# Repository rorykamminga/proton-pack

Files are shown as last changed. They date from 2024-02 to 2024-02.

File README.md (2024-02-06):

# Proton Pack
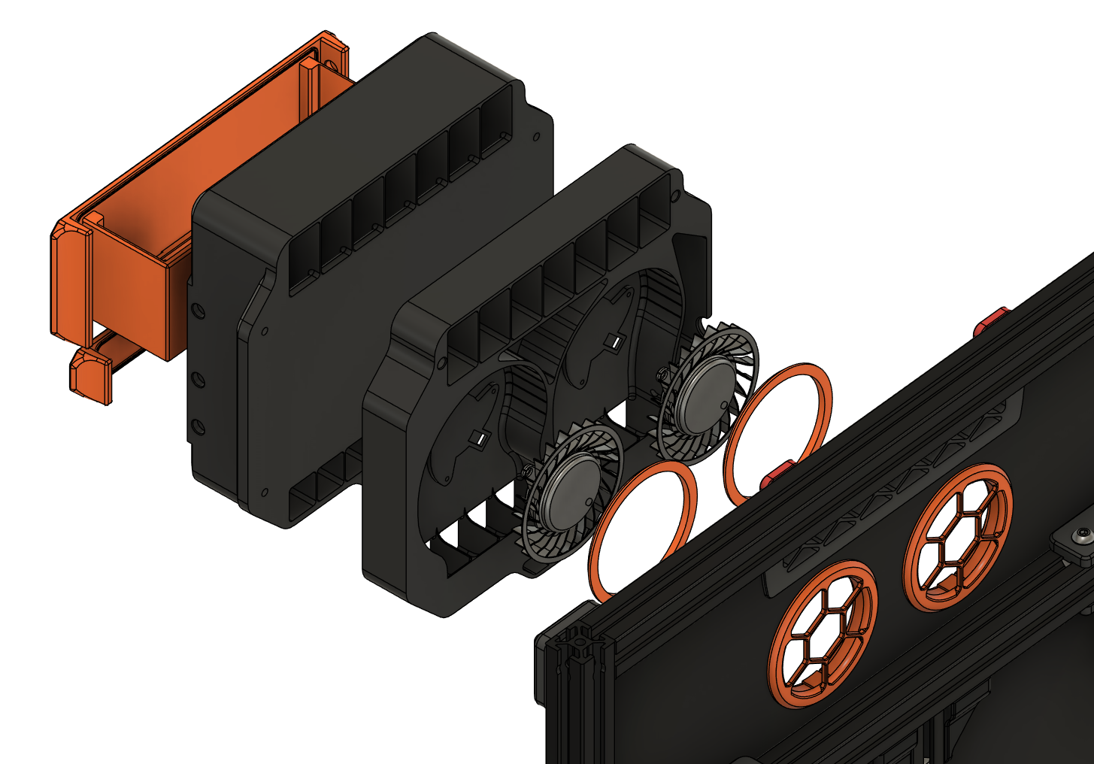
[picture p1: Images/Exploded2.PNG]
Main

## Introduction
The Proton Pack is a recirculating air filter designed for the Voron Trident.
It draws inspiration from the [Pepe Pack](https://github.com/smooshworx/pepe-pack) by smooshworx, but was ultimately sketched and built from scratch.
<br/>
## Features
- Dual 60mm blower fans for pushing bulk air
- HEPA filter for pre-filtering before carbon
- Intake thermistor mount for easy chamber temperature reading

## Bill of Materials

Qty | Item
---: | ---
2 | [Delta KFB0612HAFDB](https://www.digikey.com.au/en/products/detail/delta-electronics/KFB0612HAFDB/9974259)
1 | 119x43x9-12mm HEPA filter (for robovacs typically, this is the one I got: <https://www.aliexpress.com/item/1005002244857661.html>)
6 | M2x5mm self-tapping plastic screws
10 | M3 threaded inserts (Voron spec - 3x4x5mm)
1 | M3 roll-in nut
8 | M3x8mm bolt
3 | M3x12mm bolt\*
12 | 6x3mm round neodymium magnets (either N35 or N52 grade)
1 | Cartridge style thermistor, 3mm diameter (optional)
1 | Bag of non-acidic carbon pellets (e.g. Nevermore - see [here](https://github.com/nevermore3d/Nevermore_Micro?tab=readme-ov-file#sourcing-the-proper-acid-free-carbon) for more info on the importance of getting the right carbon)

\**note: these may need to be longer if you have thicker panels/seals, see assembly steps below*
<br/>
## Printed parts/options
**Fan Housing** - print as-is  
**Filter Housing** - select one:
- FilterHousingM6 - for M6 threaded bowden couplings (I recommend drilling these out so that the PTFE can pass through the whole fitting)
- FilterHousingM10 - for M10 threaded bowden couplings, these should already allow the PTFE to pass through completely
- FilterHousingPassthru - for passing the bowden tube through with no threaded coupling
- FilterHousingBlank - no bowden passthru, for use with internal spool holders

**Inserts** - print all:
- BasketCover
- BasketBody
- HepaCover

**Panel Shim** - print the size that matches the gasket thickness for your back panel (i.e. the thickness of the foam/rubber tape between your extrusions and back panel)  
**Fan Grilles** - print TWO of each:
- Grille that matches your panel thickness
- RetainingRing

There is also a printable ~~triforce~~ template for marking out where to drill the necessary panel holes.
This attaches to the two standard exhaust mounting points, the two holes below that indicate the centre of the 54mm intake holes, and the bottom one is for an M3 bolt to pass through.

## Printing notes
Printing the larger housing pieces can be challenging, they don't have to be ultra-strong but they *cannot* be warped or the unit will not seal.
There are also some challenging bridging and tall narrow sections that can be a pain.
I would also recommend running a skew calibration on your printer if you haven't already, since this is most noticeable on large back-to-back pieces like the two halves of the housing.

My final prototypes were printed in eSun ABS+ with 2 perimeters and 18% gyroid infill, and other than one of the vanes between the HEPA and carbon sections snapping (which I've since thickened, and also isn't really an issue) I've had no issues with it.
<br/>
## Assembly
1. Cut out the required holes on your back panel, using the provided cutting template if needed.  
   The fan intake holes need to be 54mm in diameter, and the lower mounting hole needs to allow an M3 bolt to pass through.
2. While the back panel is off, place the M3 roll-in nut on the vertical brace, just below the belts between the A/B motors (the nut hole should sit ~22mm below the top of the extrusion)
3. Clip the printed panel shim in over the nut, then replace the panel and make sure the holes line up
4. Install the fan grilles from the front, clipping on the retaining rings at the back
5. Insert 6 threaded inserts into the holes around the edges of the fan housing - 4x on the back side, 2x on the front at the top (be careful with these, as the hole is notably deeper than the insert to account for varying bolt lengths)
6. Insert the remaining 4 threaded inserts into the basket body
7. Install 6 of the magnets along the sides of the filter housing, you can use a dab of super glue if it's not a tight fit
8. Install the remaining magnets in the holes in the HEPA cover and basket cover, again using super glue if necessary (or for peace of mind)
9. Screw the basket cover onto the basket body using 4x M3x8mm bolts
10. Thread the fan wires through the cable holes and screw them down with the M2x5mm screws
11. Insert the thermistor, if using, by passing the wires down the channel on the right then pulling the cartridge into the hole
12. Trim and terminate the fan and thermistor wires with a microfit connector or similar\*
    These should have enough length to sit on the other side of the outer passthrough hold (on the side of the fan housing) for easy disconnection
13. Attach the fan housing to the back panel with 3x M3x12mm bolts (or longer if your back panel and/or sealing strips are thicker than 3-4mm) using the two standard mounting holes at the top (from inside the printer) and the third mounting hole screwing into the roll-in nut at the bottom (from the back of the printer)  
   Ensure that the housing is mounted flush to the panel, and that the shim is holding the panel flat and not causing it to bulge in or out
14. Make sure the fan wires are running along their channels, then attach the filter housing to the fan housing with 4x M3x8mm bolts
15. Insert the HEPA filter/s into the lower cavity (it should just slide in), then cover with the printed HEPA cover
16. Pour some carbon pellets into the basket (I fill mine up about 3/4), then slide it into the upper cavity
17. Screw in your bowden coupling if using, and pass through your bowden tube

\**A note on fan wires: technically you only need the red and black wires from each fan, and cut off the yellow and blue. However, I've found with these particular fans that they don't seem to like being controlled by voltage - anything below 100% and they slow down quite a lot, and below 90% they stall.*
*It may be worth keeping the PWM wire (blue) and using PWM control, but I haven't looked into it myself*

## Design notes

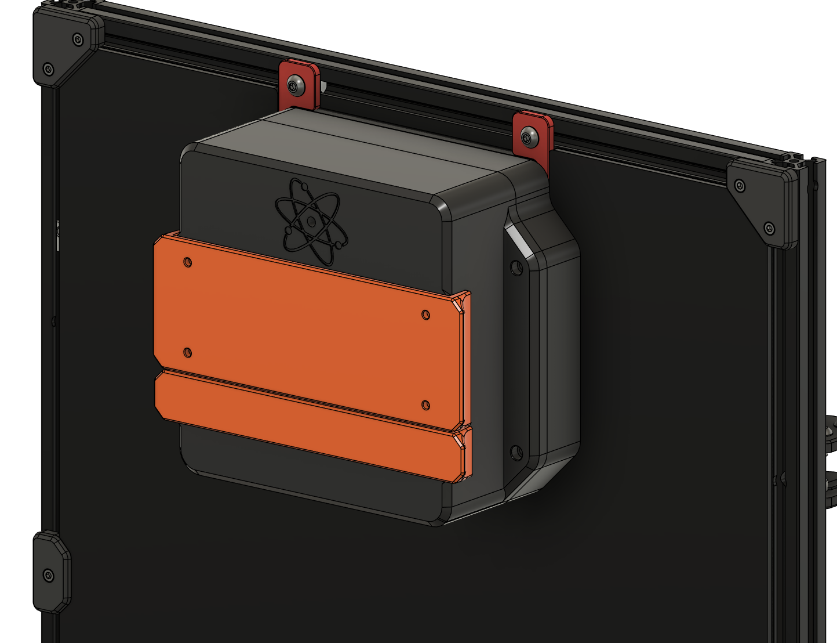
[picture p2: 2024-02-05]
Images/BackView.PNG

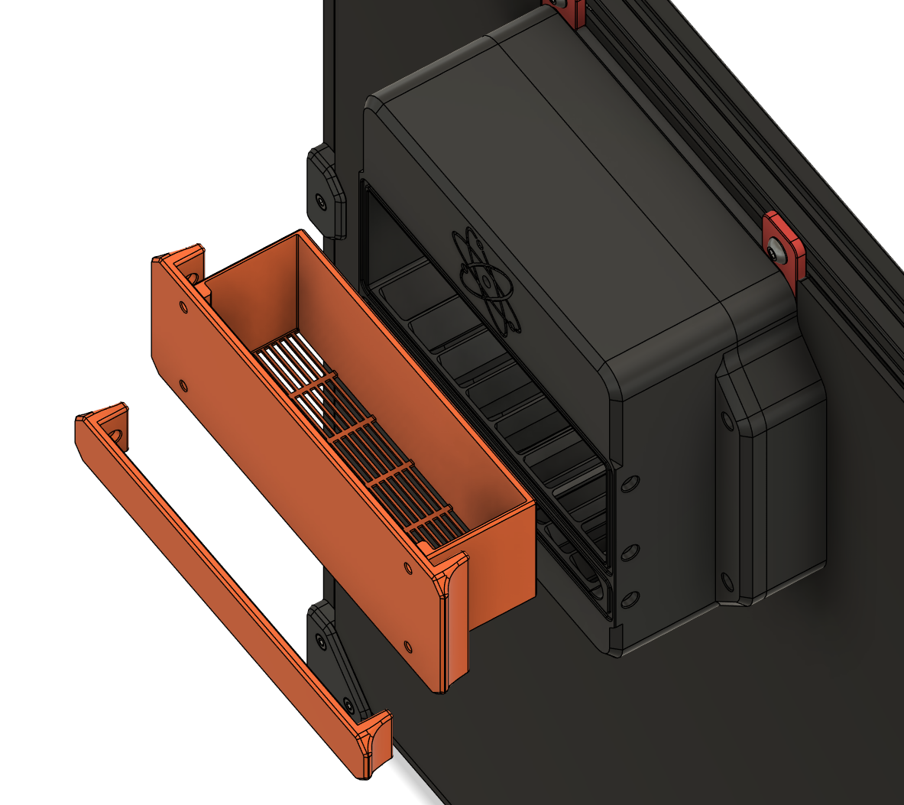
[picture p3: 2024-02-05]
Images/Exploded1.PNG

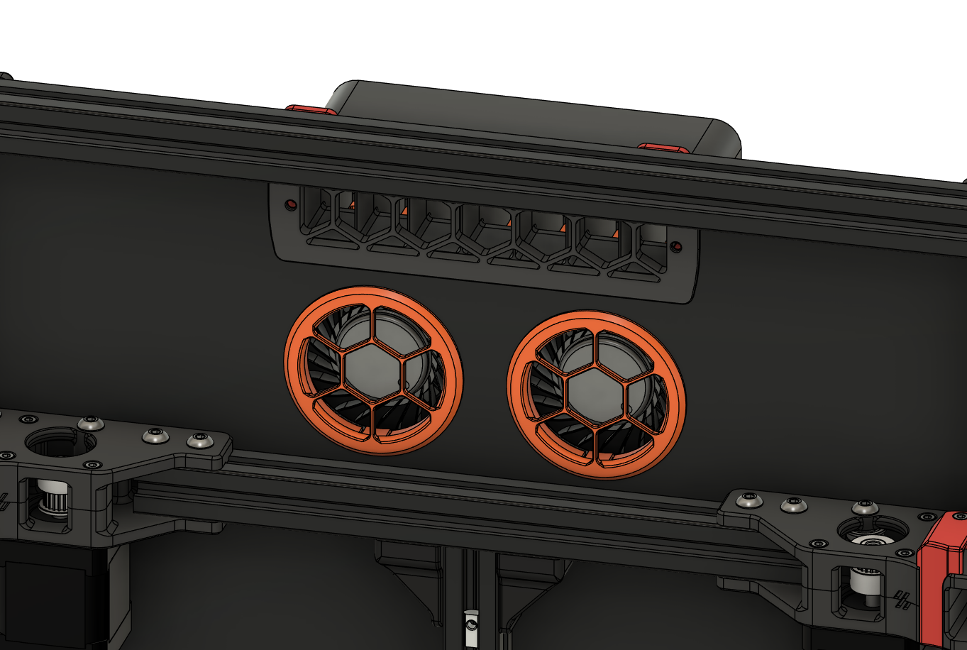
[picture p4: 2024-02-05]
Images/FrontView.PNG

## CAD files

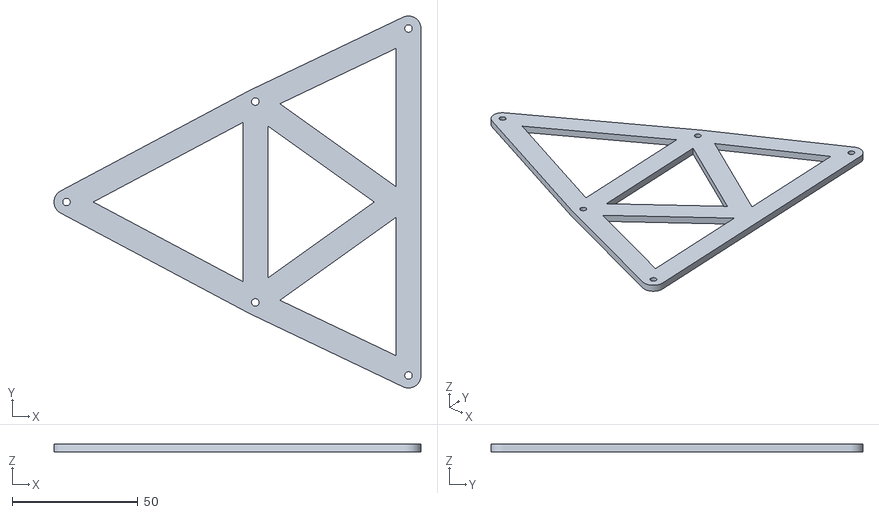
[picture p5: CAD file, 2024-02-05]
STLs/CuttingTemplate.stl
146.2 x 148.2 x 3.00

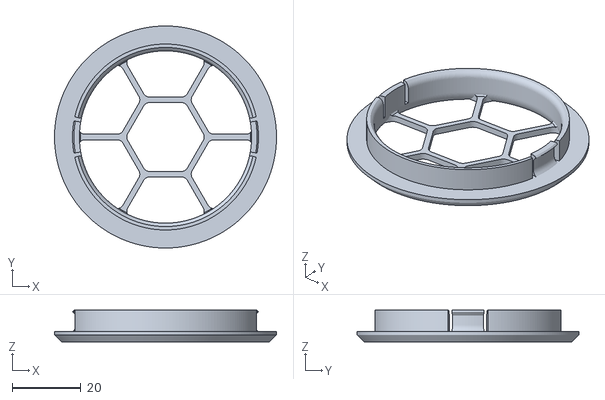
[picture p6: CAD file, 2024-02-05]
STLs/Fan Grilles/Grille3mm.stl
64.5 x 64.5 x 9.20

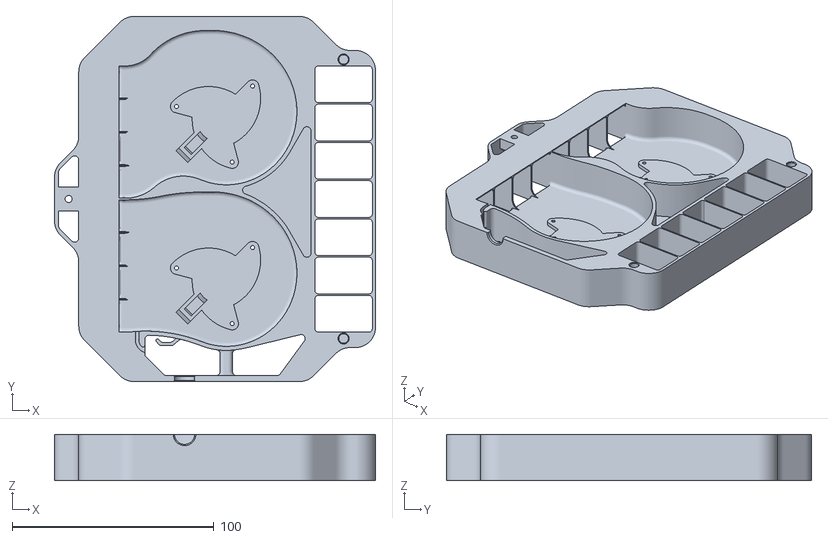
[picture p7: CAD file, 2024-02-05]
STLs/Fan Housing/FanHousing.stl
159.0 x 180.9 x 23.0

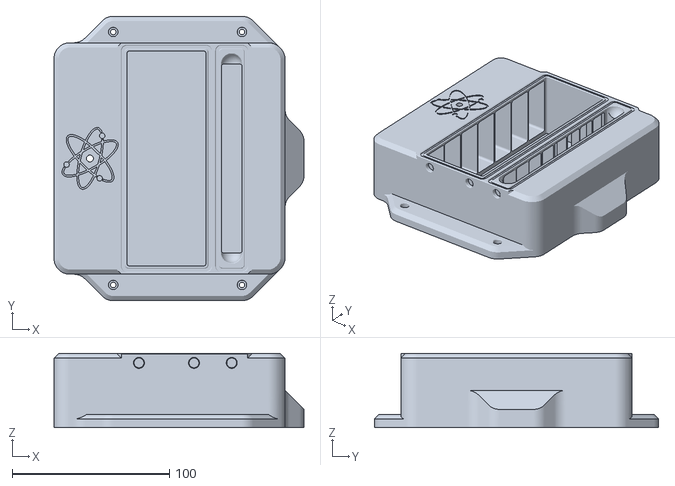
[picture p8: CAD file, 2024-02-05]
STLs/Filter Housing/FilterHousingPassthru.stl
159.0 x 180.9 x 47.1

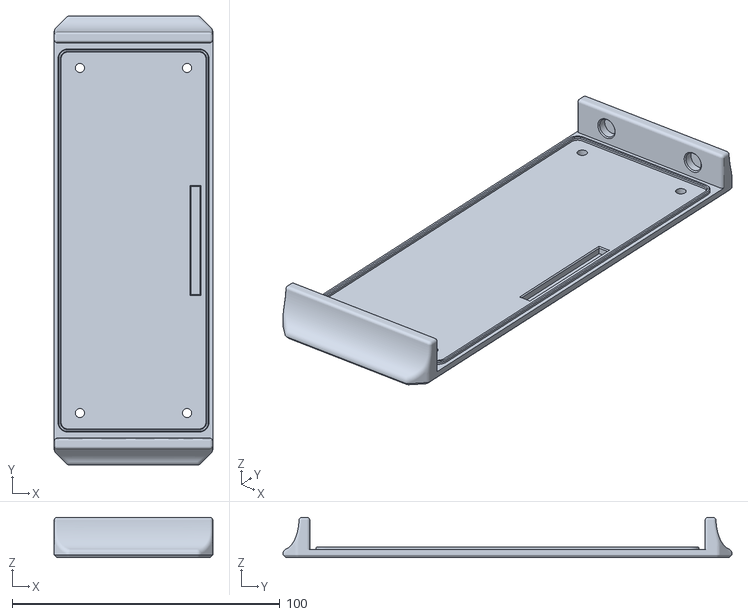
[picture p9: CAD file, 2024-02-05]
STLs/Inserts/BasketCover.stl
59.2 x 167.6 x 15.0

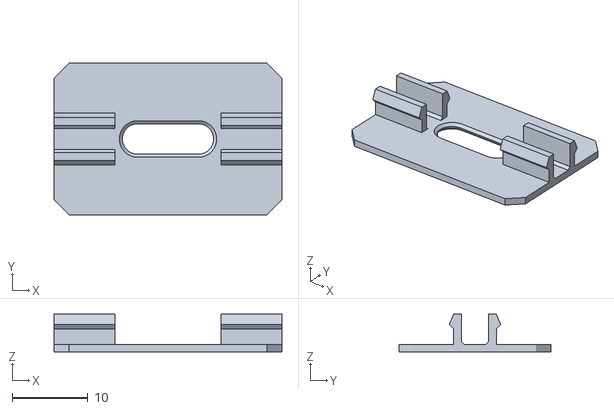
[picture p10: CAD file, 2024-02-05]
STLs/Panel Shim/Shim1mm.stl
30.0 x 20.0 x 5.00

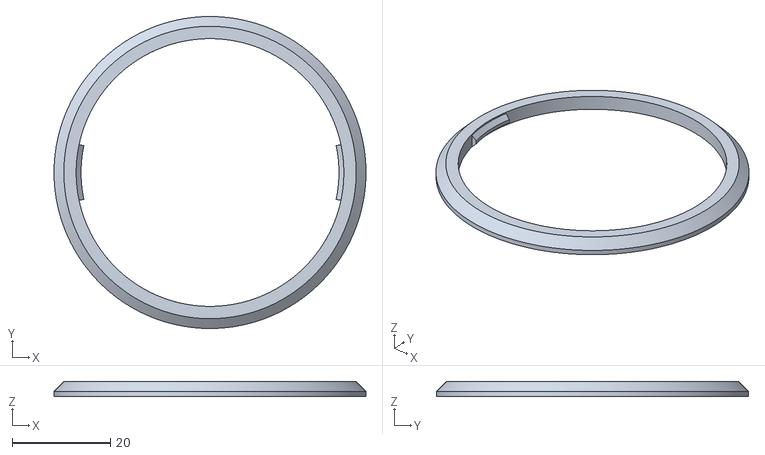
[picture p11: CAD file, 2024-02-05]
STLs/Fan Grilles/RetainingRing.stl
63.4 x 63.4 x 3.00

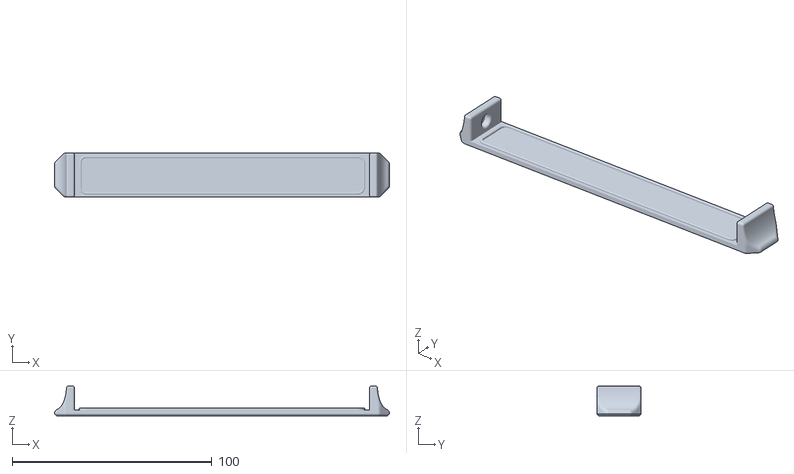
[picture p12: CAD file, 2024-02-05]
STLs/Inserts/HepaCover.stl
167.6 x 22.2 x 15.0

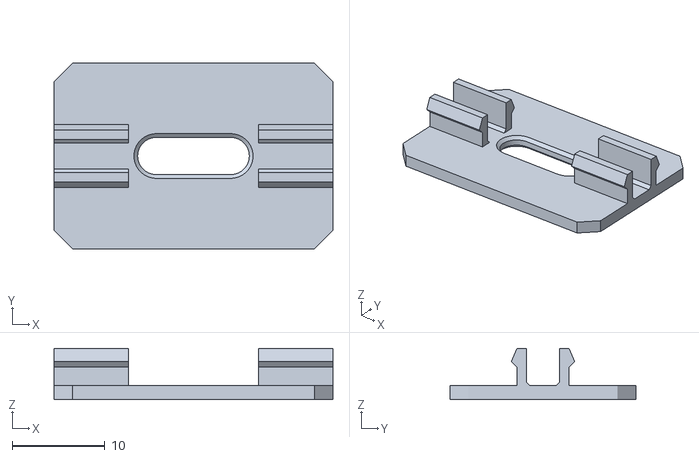
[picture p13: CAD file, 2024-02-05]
STLs/Panel Shim/Shim1.5mm.stl
30.0 x 20.0 x 5.50

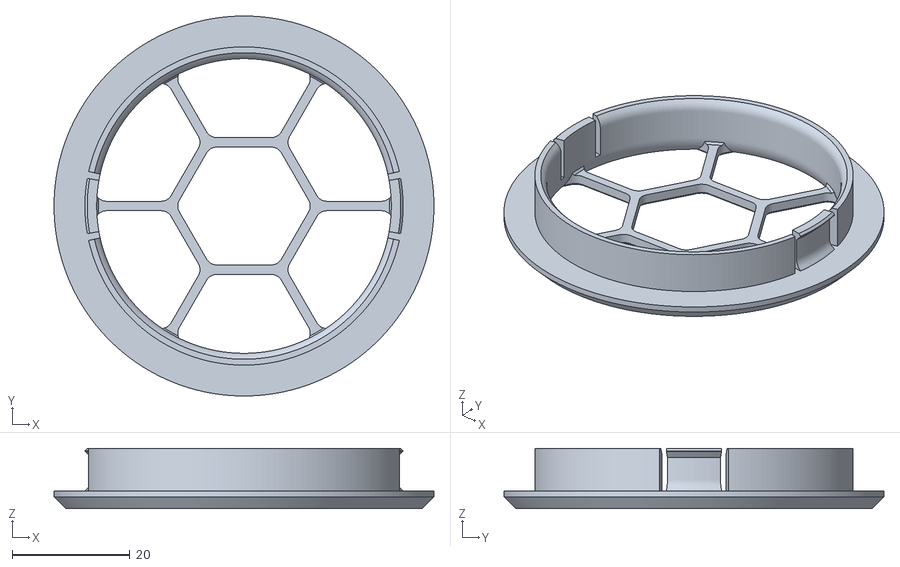
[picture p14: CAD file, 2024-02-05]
STLs/Fan Grilles/Grille4mm.stl
64.5 x 64.5 x 10.2

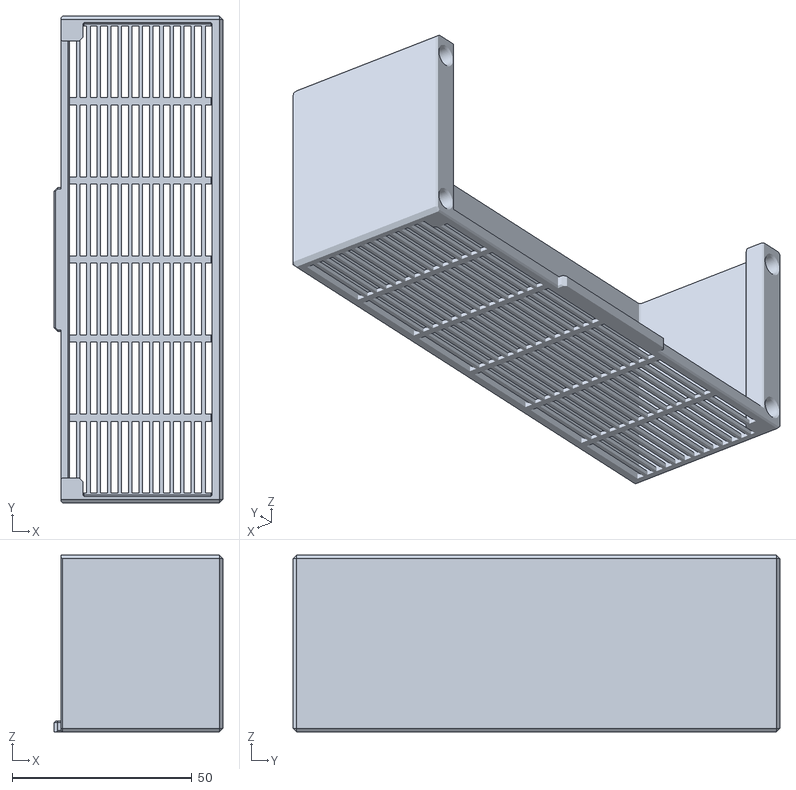
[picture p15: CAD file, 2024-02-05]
STLs/Inserts/BasketBody.stl
47.0 x 135.4 x 49.2

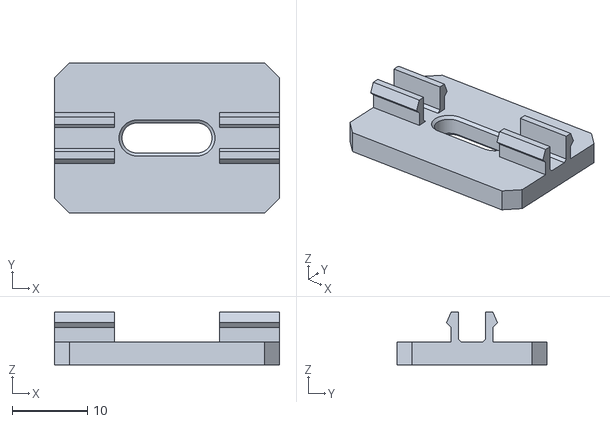
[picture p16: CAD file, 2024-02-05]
STLs/Panel Shim/Shim3mm.stl
30.0 x 20.0 x 7.00

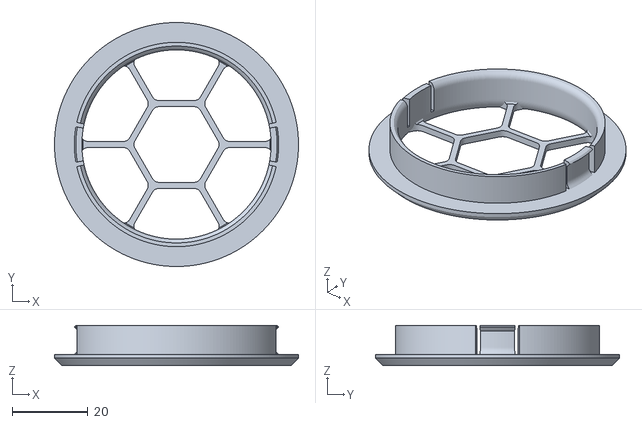
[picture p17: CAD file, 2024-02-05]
STLs/Fan Grilles/Grille4.5mm.stl
64.5 x 64.5 x 10.7

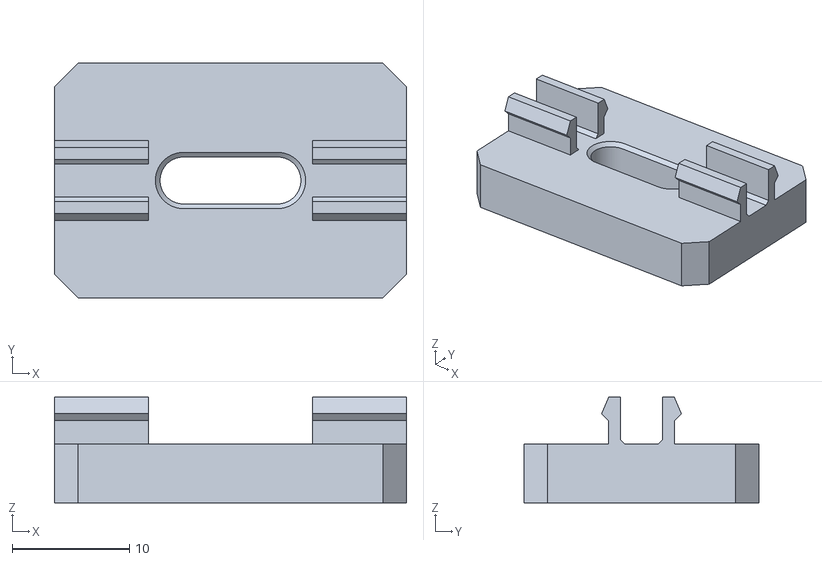
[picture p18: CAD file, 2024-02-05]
STLs/Panel Shim/Shim5mm.stl
30.0 x 20.0 x 9.00

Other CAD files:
STLs/Filter Housing/FilterHousingM10.stl
STLs/Filter Housing/FilterHousingM6.stl
STLs/Filter Housing/FilterHousingBlank.stl
STLs/Fan Grilles/Grille3.5mm.stl
STLs/Fan Grilles/Grille5.5mm.stl
STLs/Fan Grilles/Grille5mm.stl
STLs/Fan Grilles/Grille6mm.stl
STLs/Panel Shim/Shim2.5mm.stl
STLs/Panel Shim/Shim2mm.stl
STLs/Panel Shim/Shim3.5mm.stl
STLs/Panel Shim/Shim4.5mm.stl
STLs/Panel Shim/Shim4mm.stl

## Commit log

2024-02-05 Initial release
    [BasketBody.stl, BasketCover.stl, CuttingTemplate.stl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]
2024-02-06 Update README.md
    Add step for installing fan grilles
